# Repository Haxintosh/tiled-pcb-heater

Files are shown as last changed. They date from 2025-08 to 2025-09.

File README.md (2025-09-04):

render of the power distribution PCB
# Tiled 3D printing bed
This project is a scalable, Klipper-compatible heated bed system designed for efficiency and flexibility. The bed is built from PCB-based heater tiles (≈100W each) that can be individually powered, allowing selective heating to reduce energy use. A central hub board, driven by an STM32 microcontroller, controls up to multiple channels with individual MOSFET switching and thermistor sensing.  

The project consists of 2 types of PCBs, the tiles and the power distribution boards.  

Currently there is a 150mm tile and a 8 channel power distribution board.  

## Images
Heater tile:  
render of the tile  
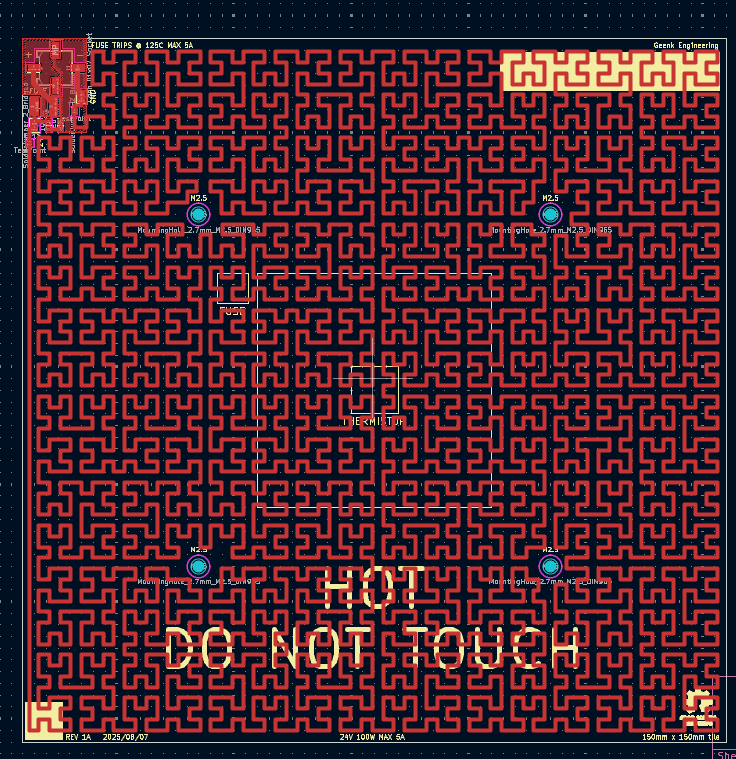
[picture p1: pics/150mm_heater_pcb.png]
image of the pcb
  
Power distribution board:  
render of the power distribution PCB  
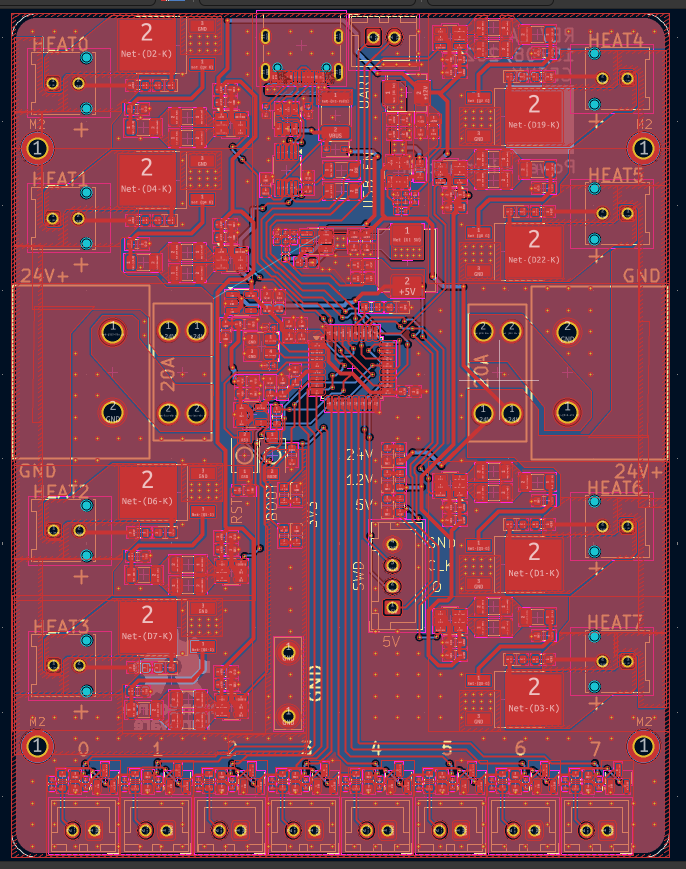
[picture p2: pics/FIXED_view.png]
image of the pd pcb
  

## Specs
The calculator can found here: https://www.desmos.com/calculator/dyaic1mb9s  

Per tile:
| Measurements 	| Value 	|
|---	|---	|
| Dimensions 	| 150mm x 150mm 	|
| Power			| ~110W @ 24v 	|
| Max Temp		| ~105°C*			|

> [!WARNING]
> The max operating temperature depends on the rated temperature of the connector. The thermal fuse blows at around 125°C to prevent thermal runaway, but the current chosen connector (MicroFit 3) is only rated to 105°C.

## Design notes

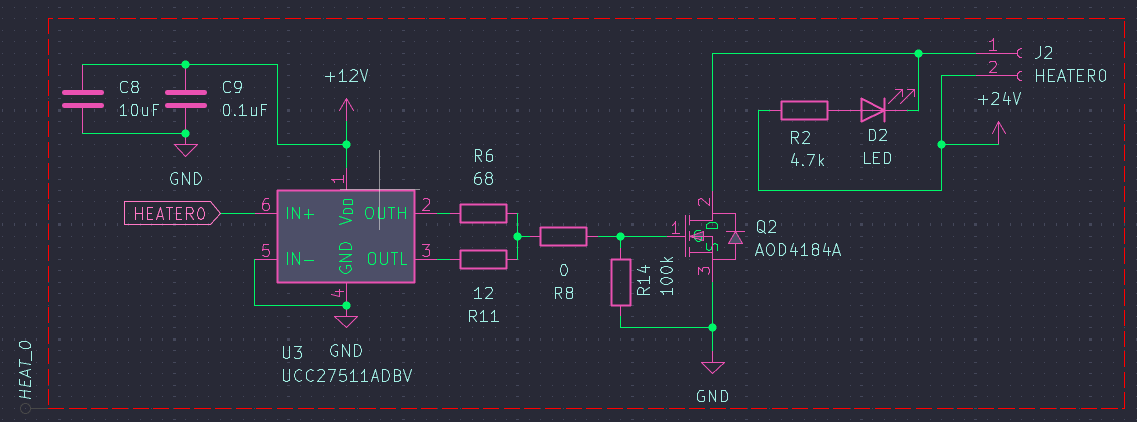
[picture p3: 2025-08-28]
pics/labeled.png

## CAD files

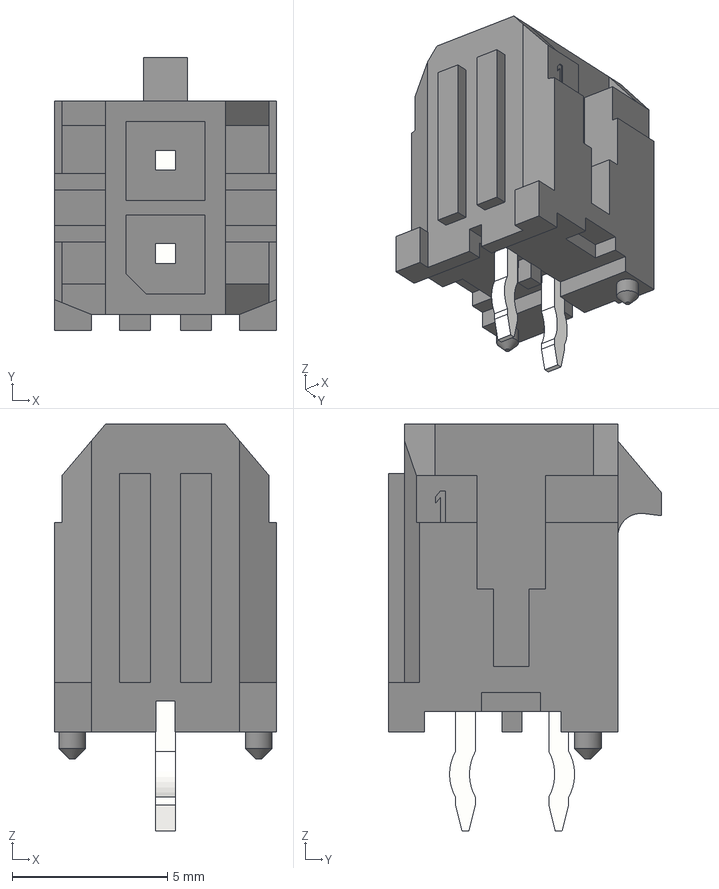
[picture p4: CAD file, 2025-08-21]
src/power distribution/3d/430450212.step
7.15 x 8.77 x 13.1 mm

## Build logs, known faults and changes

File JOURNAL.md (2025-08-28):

---
Title: "Modular 3D printing bed"
Author: "Geenk"
Description: "A modular and scalable 3D printing heated bed system."
Created On: "7/8/2025"
---

# 2025-08-07 Log 1: Initial planning & research
Time: 30min  
Started the project and laid out the project's main criteria. The project is a Klipper compatible scalable and modular heated bed system. The tile nature of the beds allows the printer to selectively heat areas to reduce power consumption. The heated beds are made of individual tiles of PCB-based resistive heaters, which are connected to a power distribution board/hub. The hub, in turn, is connected to Klipper via UART over USB and is able to control 8 tiles of around 100W each. Each tile is connected through a connector for power and another one for thermistor (maybe add a connector on the tile for a thermistor to allow for a single cable from tile to hub? interference). To calculate the length and the width of the trace required for a given wattage, I've found and used the trace resistance formula and put it in a Desmos calculator (https://www.desmos.com/calculator/dyaic1mb9s).   
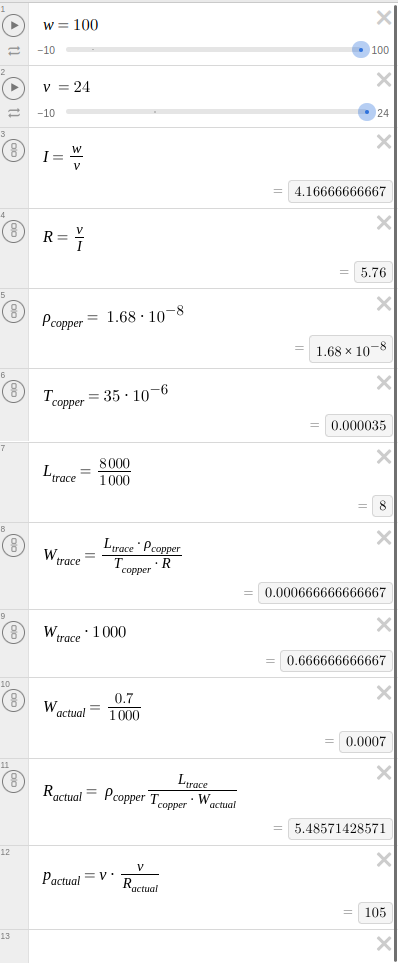
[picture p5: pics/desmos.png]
desmos image of trace width and height calculations


# 2025-08-07 Log 2: Heated bed schematic
Time: 30min  
Finished the schematic of the heated bed. I've decided to add in a thermal fuse in series with the 24V input to prevent the heater to go into thermal runaway. I have also added a LED to indicate when the plate is being powered. It was hard to figure out a way to connect a single trace to 24V and GND without screwing up the nets  of the PCB. I've tried tying 24V and GND but that resulted in everything being named GND and I also tried making the trace resistor into a component, but that didn't work since I needed to modify its' traces for things like screw holes. I finally decided on using solder jumpers to isolate the heater traces. For the connector, I've settled on a Molex MicroFit 3 since some of the connectors are rated up to 125C.   
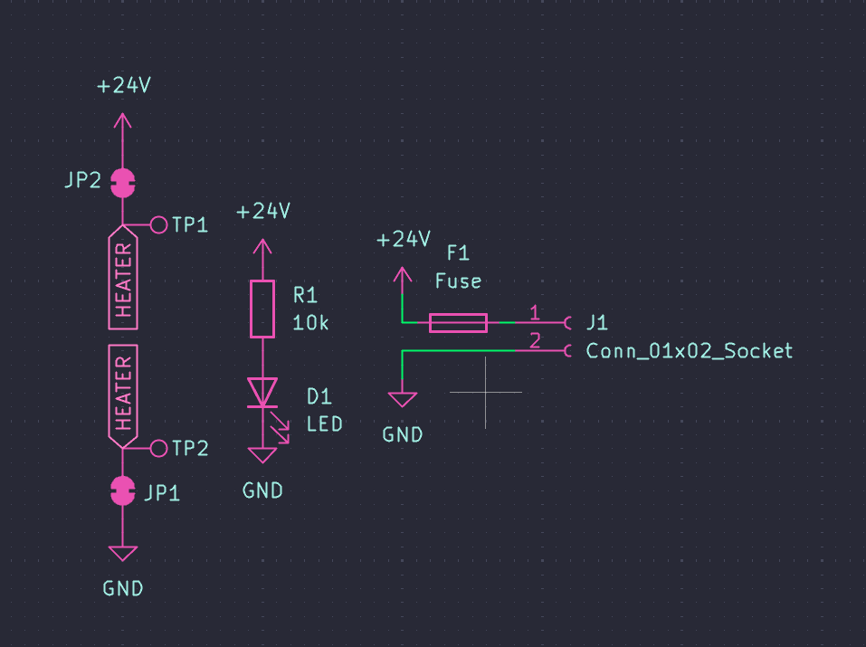
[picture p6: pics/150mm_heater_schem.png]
schematic of the 150mm heated bed
  

# 2025-08-08 Log 3: Heated bed PCB
Time: 1.5h  
Laid out the Hilbert curve heater trace using the KiCad space filling curve plugin, also finished most of the layout of the PCB (LED, connector, fuse). All components and traces are single sided since I plan on going with the aluminum PCB at JLCPCB.  

# 2025-08-08 Log 4: Finalize Heated bed PCB
Time: 1h  
Finalized the heated bed PCB. I added M2.5 holes for mounting and had to move the Hilbert curve traces for hole and countersink clearances. Ran DRC and fixed many errors related to the Hilbert curve since I generated it a bit too big. I added also some silkscreen texts.  
PCB image of the heated bed PCB
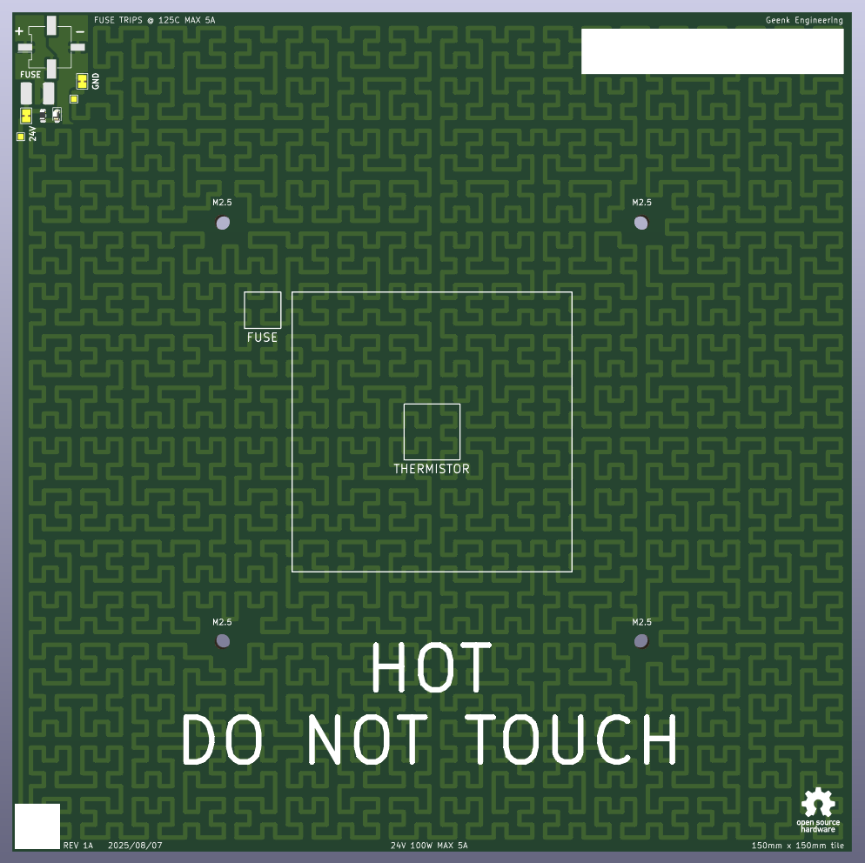
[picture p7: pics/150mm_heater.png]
rendered image of the heated bed PCB
  
# 2025-08-11 Log 5: Power distribution schematic (MCU + MOSFET drivers)
Time: 2h  
Started the schematic for the power hub board. The board is made up of 4 main sections, the MCU, STM32F030K, was chosen due to its analog input multiplexing capabilities and its ease of integration with Klipper, the MOSFET switching, made up of a gate driver and a N channel MOSFET capable of handling up to 5A of current with safety margins, the thermistor sensing section, and finally the voltage rails. I've finished most of the MCU section, with the UART to USB converter, the crystal oscillators, and the pinout of the MCU. I've also done the MOSFETs, where each one is controller by a driver IC and there's 8 channels of switching. It was my first time working with STM32 chips but it was easier than I thought.  
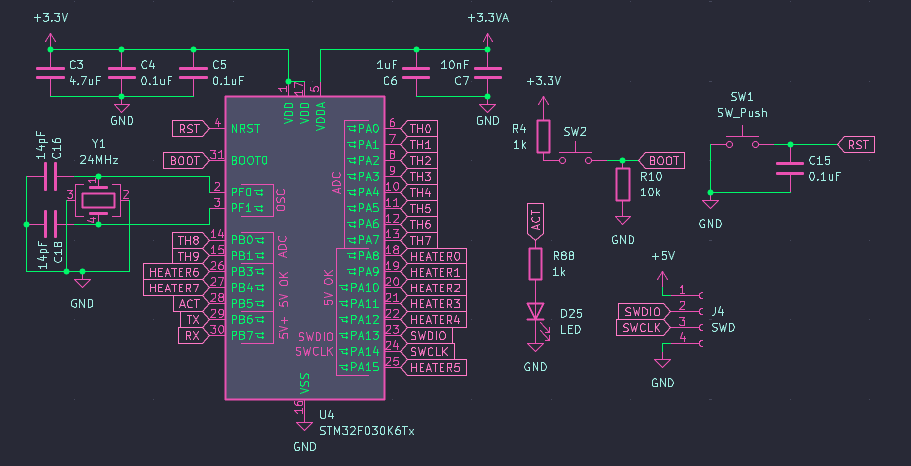
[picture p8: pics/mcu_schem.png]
schematic of the STM32 MCU

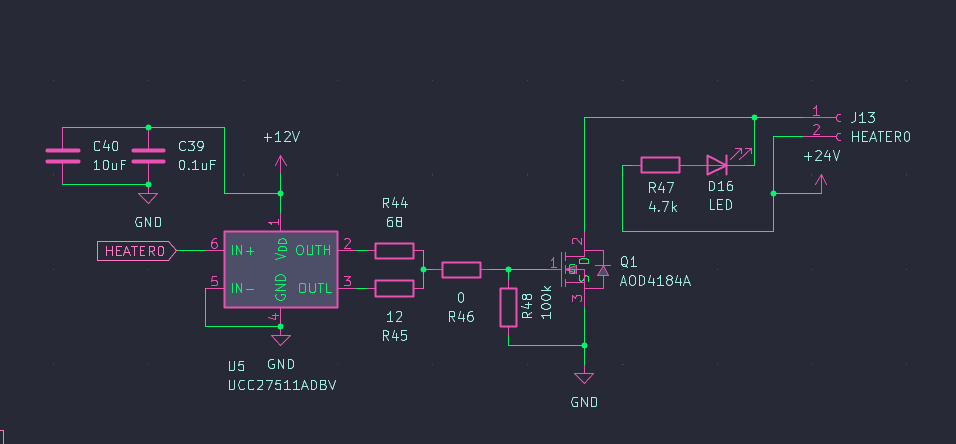
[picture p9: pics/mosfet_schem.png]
schematic of the MOSFET and the gate driver
  

# 2025-08-12 Log 6: Power distribution schematic (thermistor sensing, power rails, and a bit of clean up)
Time: 2h  
Finished up the schematic for the power distribution board. I've added in the thermistor sensing section and the voltage rails needed to power the board. Also added some protection in the form of a polyfuse on the USB rails and one fuse on each of the 24V input rail just in case. The thermistor sensing as derived from the BTT SKR mini E3 since it's an established design that  probably will work and I don't wanna spend hours debugging an analog circuit. The power rails are divided up into 24V for the heaters, 12V for gate driver power and allows the MOSFET to fully open, 5V for peripherals and powers the 3V3 rails. The 3V3 rails are divided up into analog 3V3 and digital 3V3 to minimize noise in the thermistor readings.   
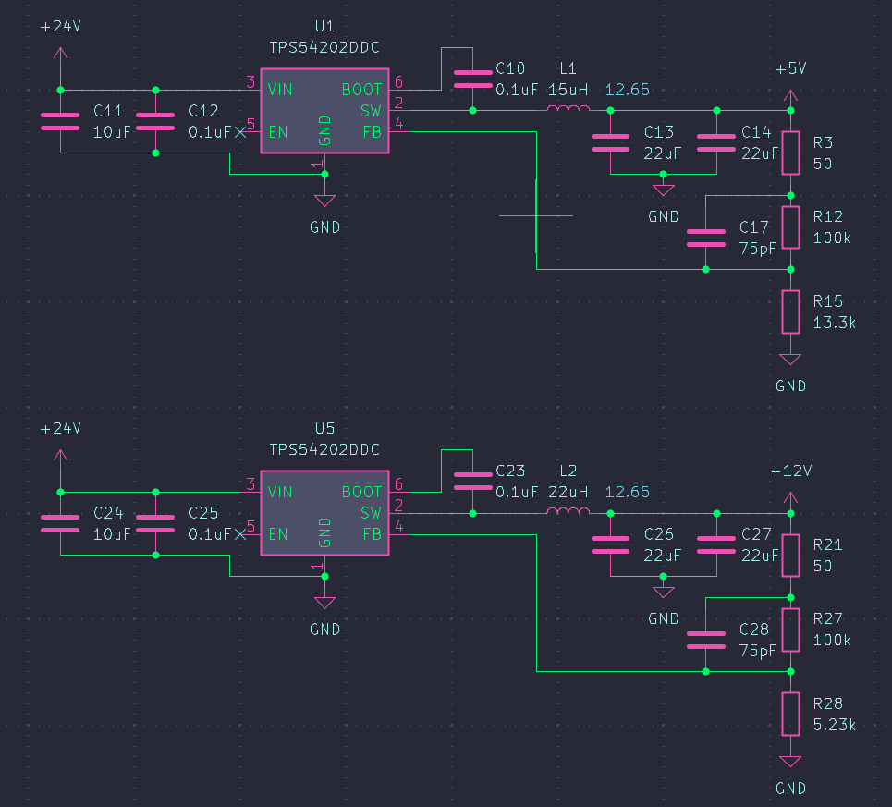
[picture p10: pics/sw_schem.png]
schematic of the switching regulator for the 5V and 12V

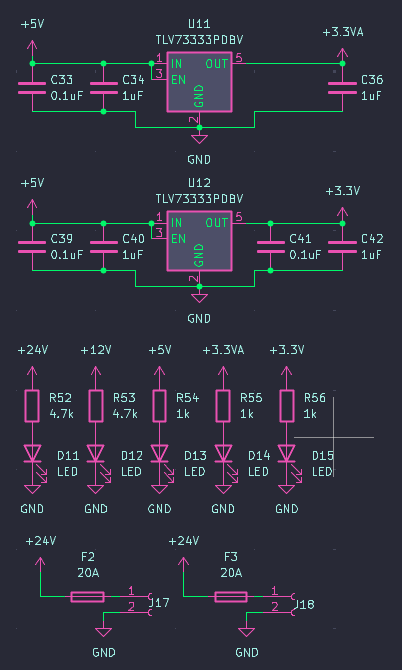
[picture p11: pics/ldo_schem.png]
schematic of the LDOs and led indicator for power

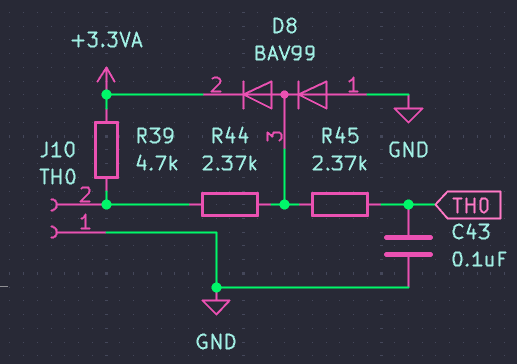
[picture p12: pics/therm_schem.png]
schematic of the thermistor sensing section
  

# 2025-08-16 Log 7: MOSFET channel placement  
Time: 3.5h  
Started on the PCB layout for the power distribution board. The idea was to have 4 outputs on the left and right side of the PCB with a power input screw terminal in the middle of the 4 outputs. I thought I could save time by using the multichannel placement tools recently added to KiCad, but I didn't know how to use it at first for sheets without hierarchical sheets. But after 30min of experimentation, I figured it out and annotated the schematic with rule areas and directive labels. Then, I routed laid out a MOSFET switching channel, making sure there's plenty of thermal mass in the copper planes surrounding the MOSFET to take away the heat for thermal management. Then, after finishing a single channel, I've replicated the single channel design to 3 other channels for the left side. I've then moved them around a bit to fit the power connector in the middle. Then I had to extend some of the copper planes to connect the other channels. I then did the same for the right side.   
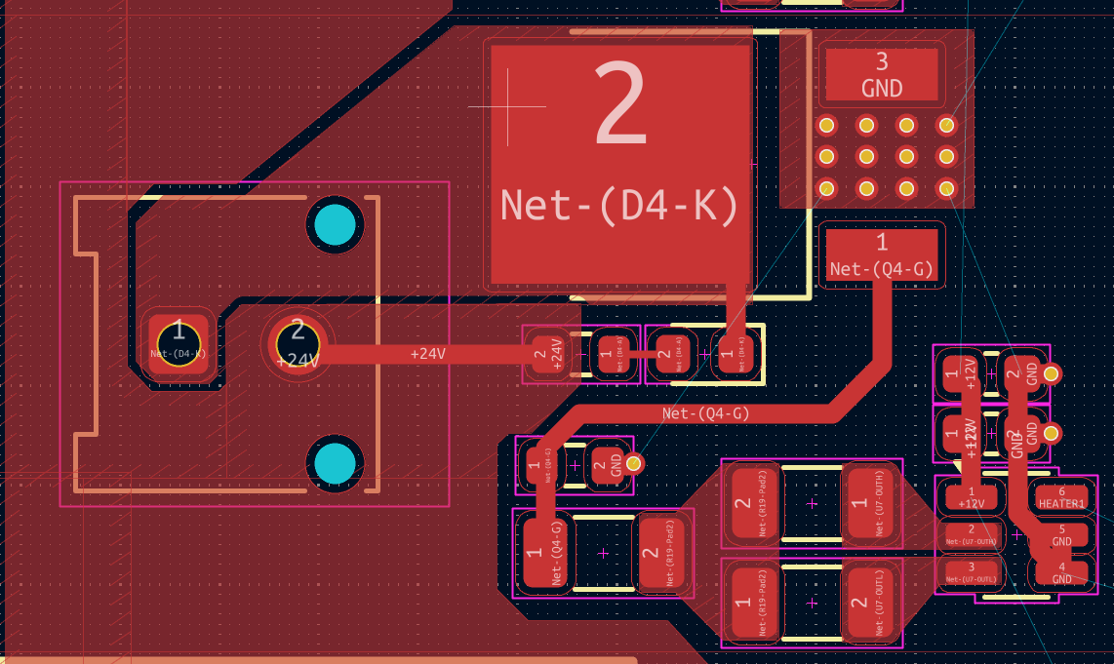
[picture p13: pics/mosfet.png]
image of a single MOSFET layout

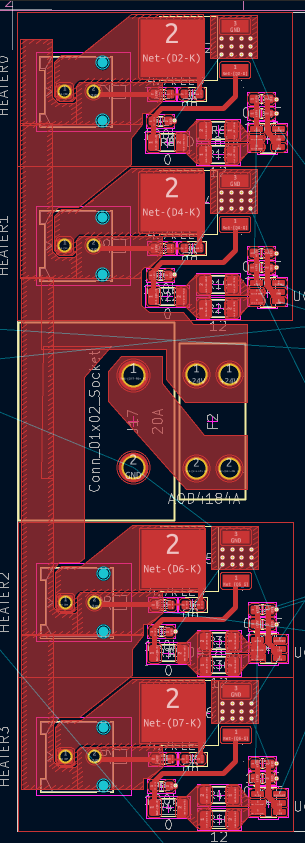
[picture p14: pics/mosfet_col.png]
image of the complete MOSFET layout for the left


# 2025-08-17 Log 8: USB, protection and UART-USB
Time: 1h  
Laid out the PCB for the USB C connector and the ESD protection circuitry, Also routed the polyfuse. The layout for the UART to USB was also done. I included a connector and some 0 Ohm resistors in series with the UART bus for a direct Klipper UART connection option.  
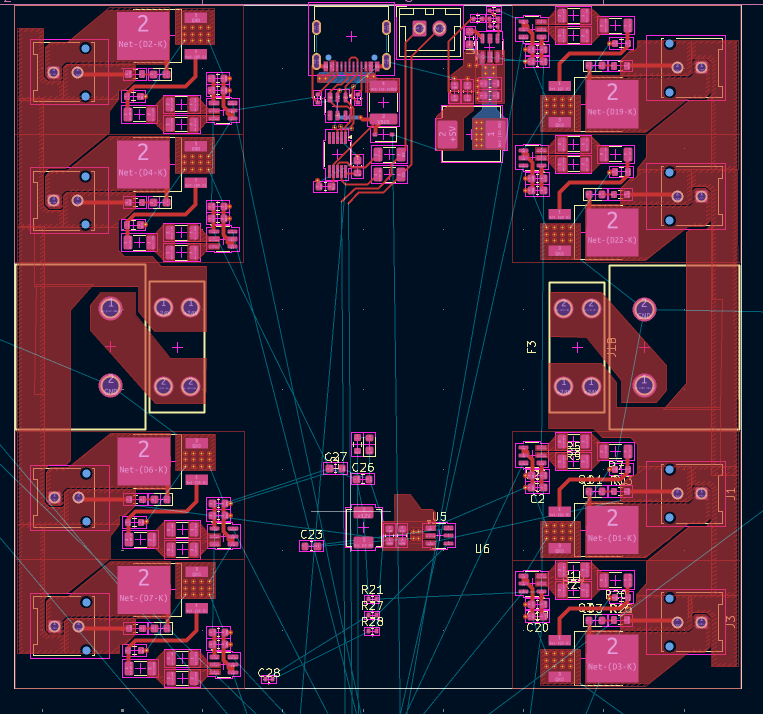
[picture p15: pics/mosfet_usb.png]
image of the whole PCB with the MOSFET layout and USB layout on top
  

# 2025-08-18 Log 9: Power regulation
Time: 1.5h  
Laid out the traces for the voltage regulators. The 5V and 12V rails are converters from 24V using switching regulators. I had to plan things out with the MCU to not interfere with the analog traces especially given the high noises originating from tshe switching regulators. The feedback resistors were placed far away from the switching nodes and most of the layout followed the recommended layout by TI.   

# 2025-08-18 Log 10: STM32
Time: 1.5h  
Placed the MCU in the middle of the board, with the sensitive analog pins facing towards to bottom of the board and away from the switching regulators. Then the decoupling capacitors were placed along side the crystal oscillator. I then placed the 2 LDOs regulating the 3V3 rails quite close to the STM32 since there weren't many places left for them. I then connected the PWM control signals for the MOSFETs. I originally thought that the PWM traces from the MCU will cause a good amount of noise, but apparently Klipper uses a 10Hz signal to control   the heaters. 
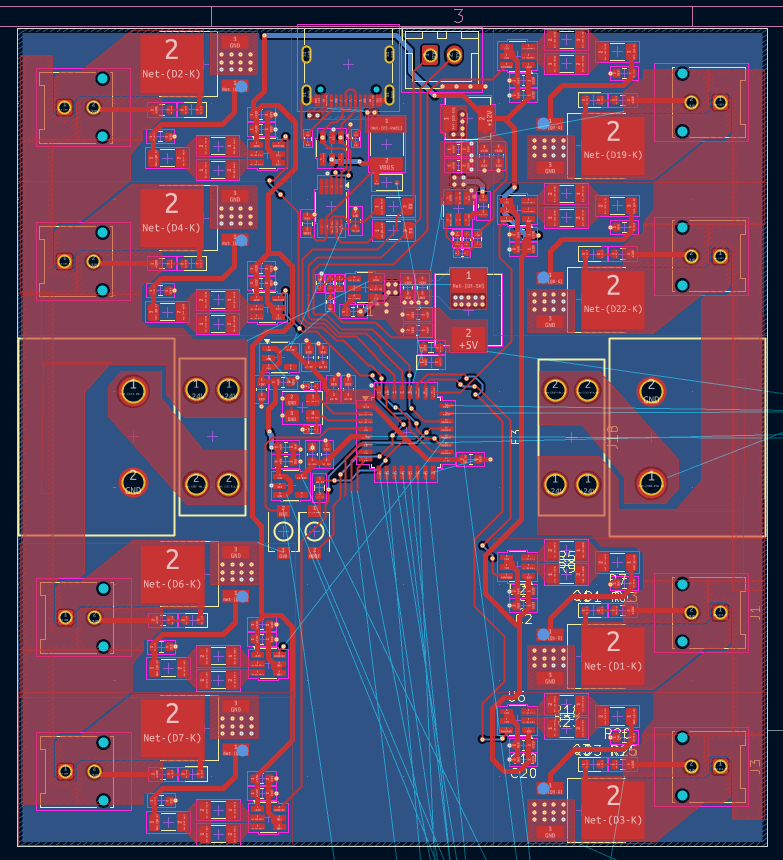
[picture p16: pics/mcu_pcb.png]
image of the whole PCB with the MCU section done


# 2025-08-20 Log 11: Thermistor & DRC
Time: 2h   
Routed the thermistor sensing section on the PCB and replicated the layout for the other 7 channels. Then routed from the MCU to the channels. I've also placed the SWD connector for debugging and for flashing just in case the USB flashing fails. I've also added a test hook for oscilloscope ground for probing purpose. I've also added some M2 screw mount holes on the 4 corners of the PCB and silkscreen labels for the different inputs and LEDs. I finished by rounding out the corners of the PCB and ran & fixed DRC.  
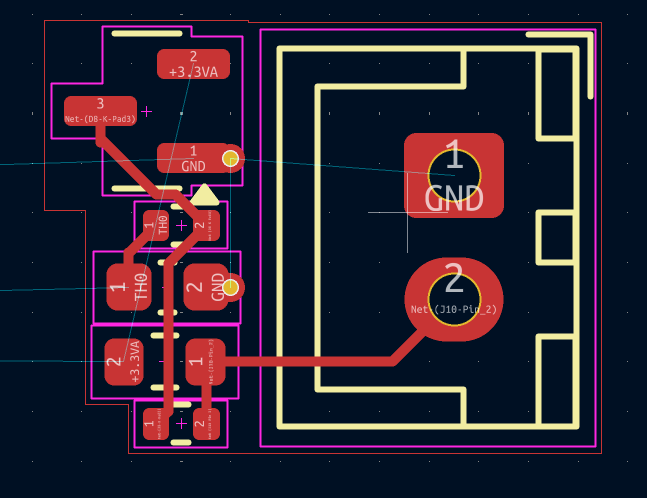
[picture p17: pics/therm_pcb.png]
image of the themistor sensing layout

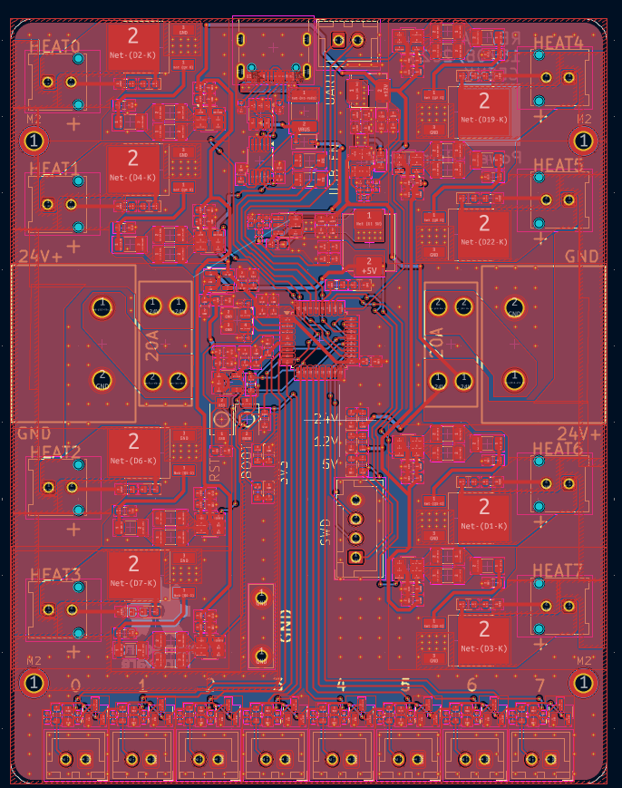
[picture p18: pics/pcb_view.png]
image of the finished PCB


# 2025-08-21 Log 12: UART issue
Time: 30min  
Found out that the for STM32 to flash over USB using a USB-UART converter, the pins PA9/PA10 must be used for UART. I was using a different set of pins, meaning that I would not be able to flash the STM32 via USB. I switched and rerouted the HEATER1-2 pins with the UART RX/TX pins.   
image of the fixed PCB
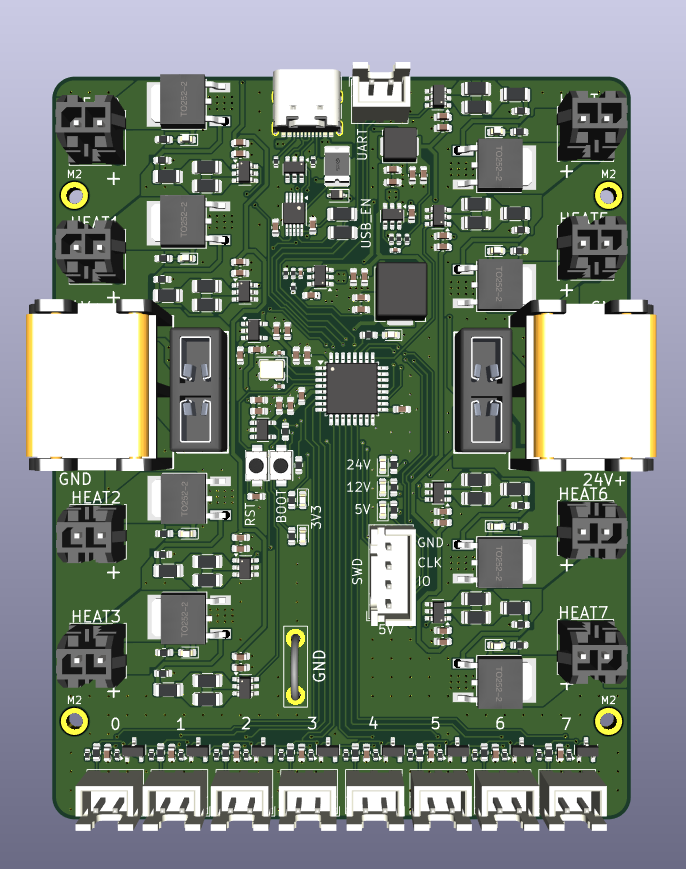
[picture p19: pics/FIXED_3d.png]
image of a 3D view of the PCB


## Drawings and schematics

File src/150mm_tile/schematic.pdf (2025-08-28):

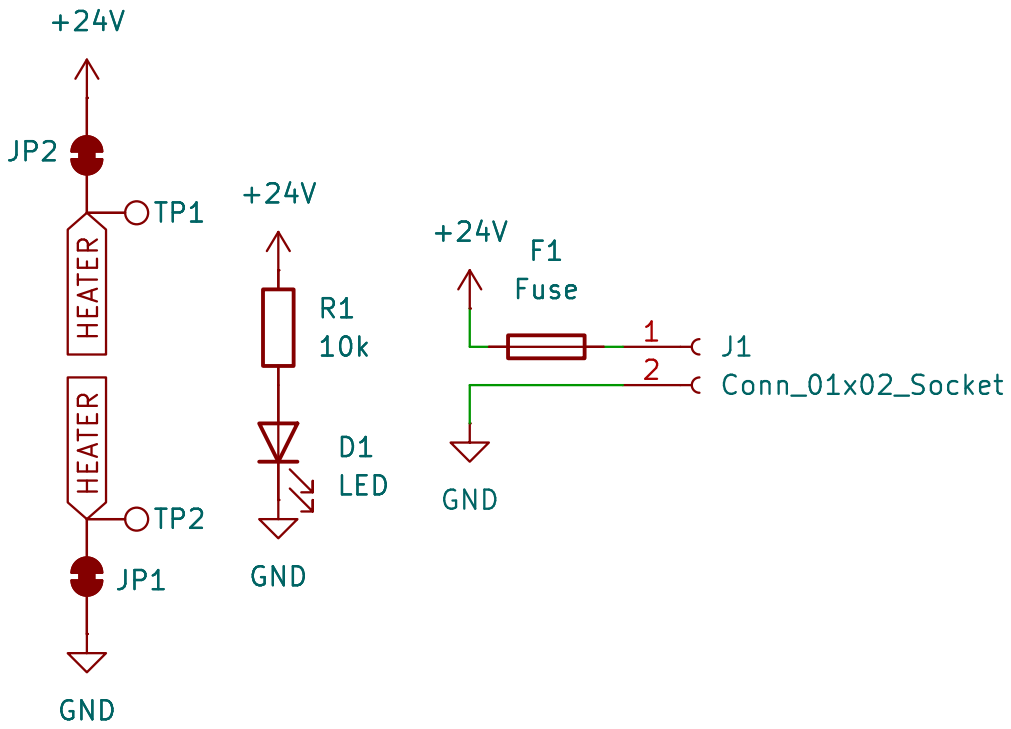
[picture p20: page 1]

Id: 1/1 Title: File: pcb-heater.kicad_sch Sheet: /

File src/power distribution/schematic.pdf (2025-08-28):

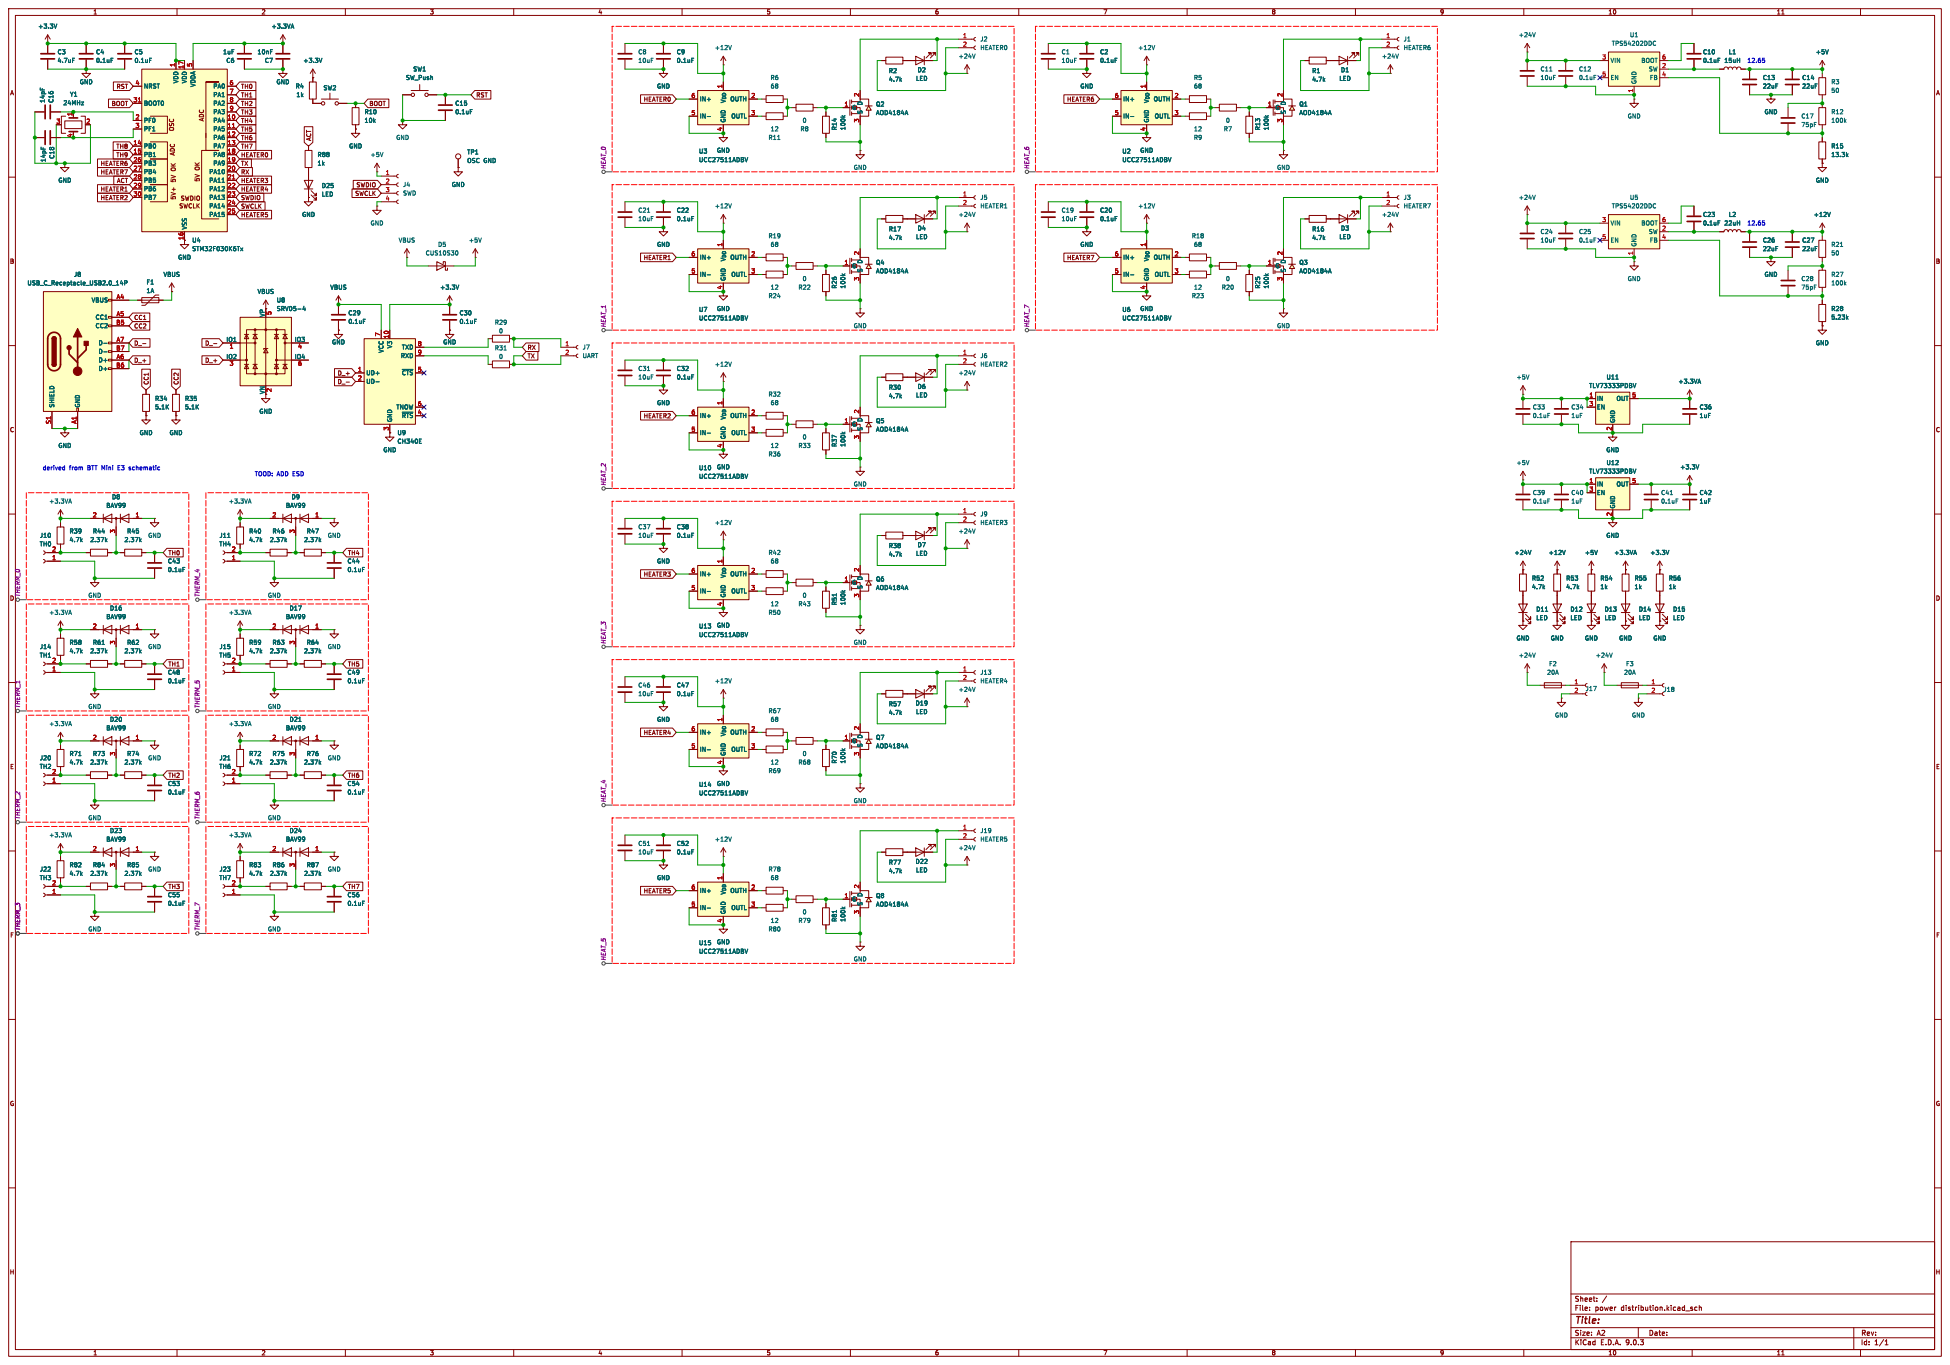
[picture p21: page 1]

TH8 BOOT
SWDIO5V OK ADC
LED OSC ADC 5V OK 5V+ SWCLK

derived from BTT Mini E3 schematic

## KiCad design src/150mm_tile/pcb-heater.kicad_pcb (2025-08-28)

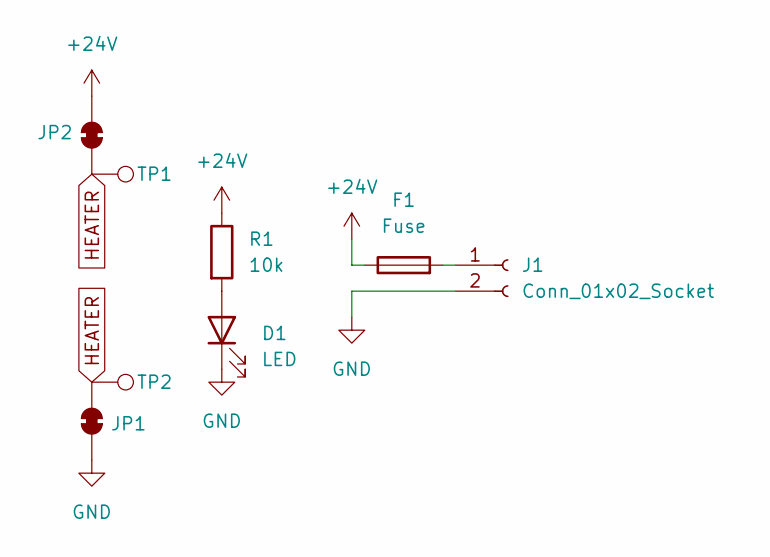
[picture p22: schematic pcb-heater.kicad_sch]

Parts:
D1: LED; LED_0603_1608Metric
F1: Fuse; thermal fuse
J1: Conn_01x02_Socket; Molex_Micro-Fit_3.0_43045-0218_2x01-1MP_P3.00mm_Vertical
JP1, JP2: SolderJumper_2_Bridged; SolderJumper-2_P1.3mm_Bridged_Pad1.0x1.5mm
R1: 10k; R_0603_1608Metric
TP1, TP2: TestPoint; TestPoint_Pad_1.0x1.0mm

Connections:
+24V: F1.1, JP2.1 (A), R1.1
GND: D1.1 (K), J1.2, JP1.1 (A)
HEATER: JP1.2 (B), JP2.2 (B), TP1.1, TP2.1
unnamed: D1.2 (A), R1.2
unnamed: F1.2, J1.1, J1.MP

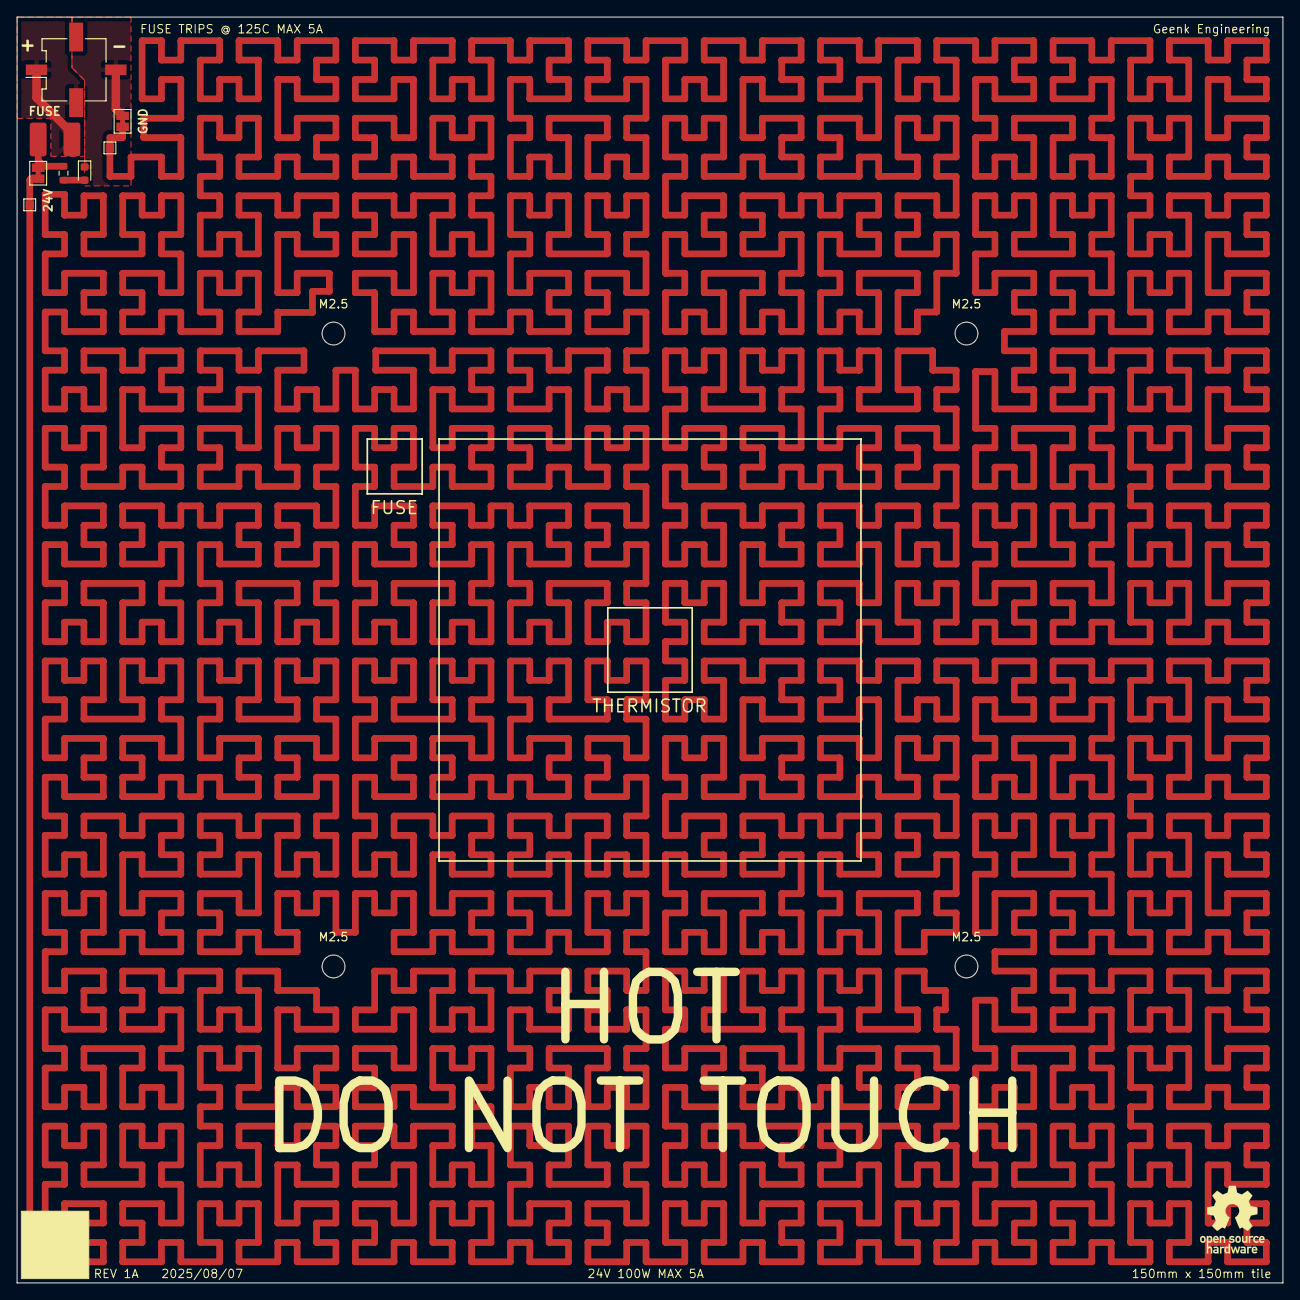
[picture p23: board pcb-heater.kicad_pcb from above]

Board: 2 copper layers, 150.0 x 150.0 mm, 12 parts (0 on the bottom side), 5 nets.

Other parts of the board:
M2.5, M2.5#2, M2.5#3, M2.5#4: MountingHole_2.7mm_M2.5_DIN965

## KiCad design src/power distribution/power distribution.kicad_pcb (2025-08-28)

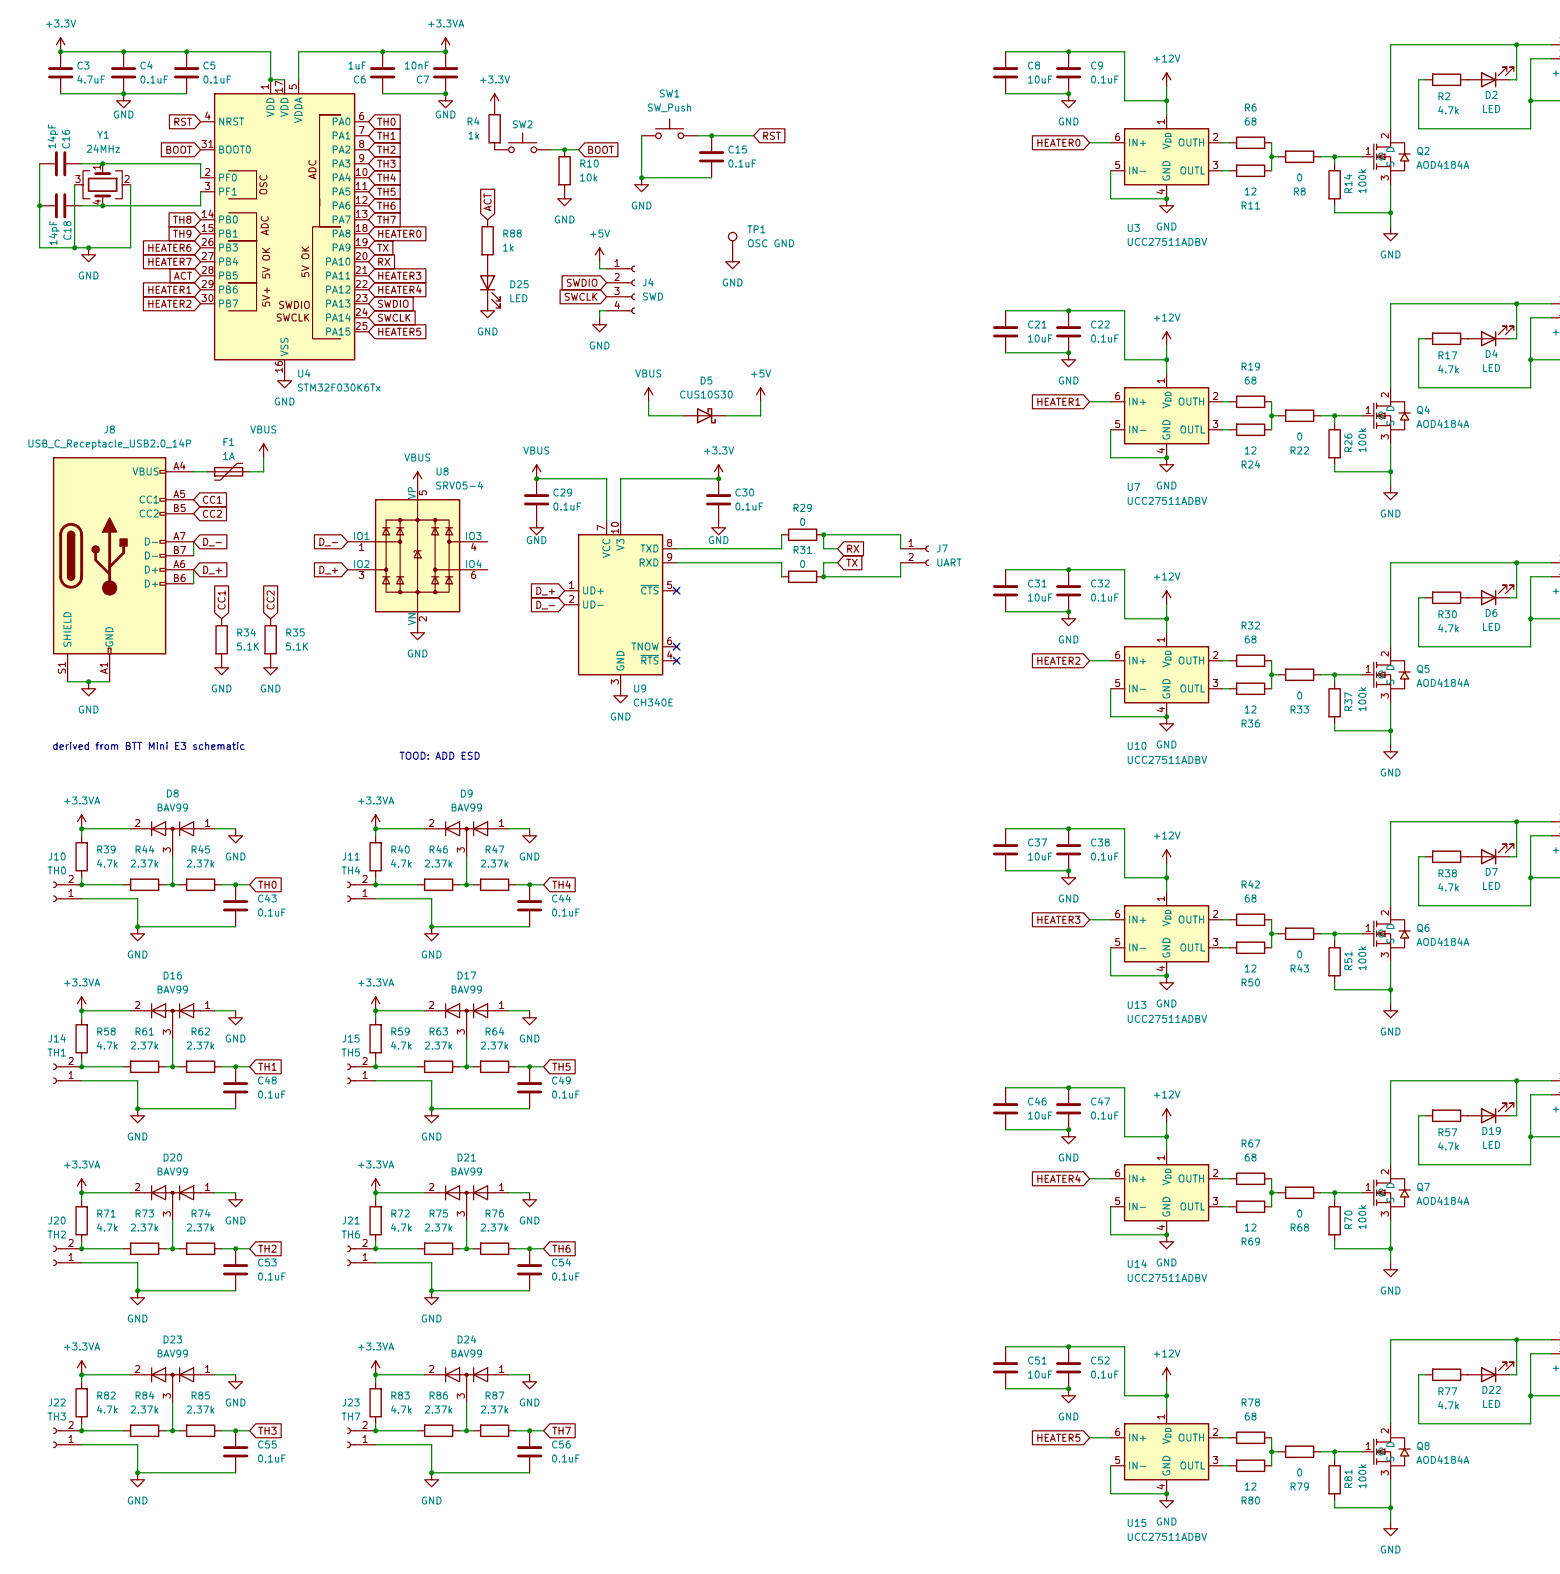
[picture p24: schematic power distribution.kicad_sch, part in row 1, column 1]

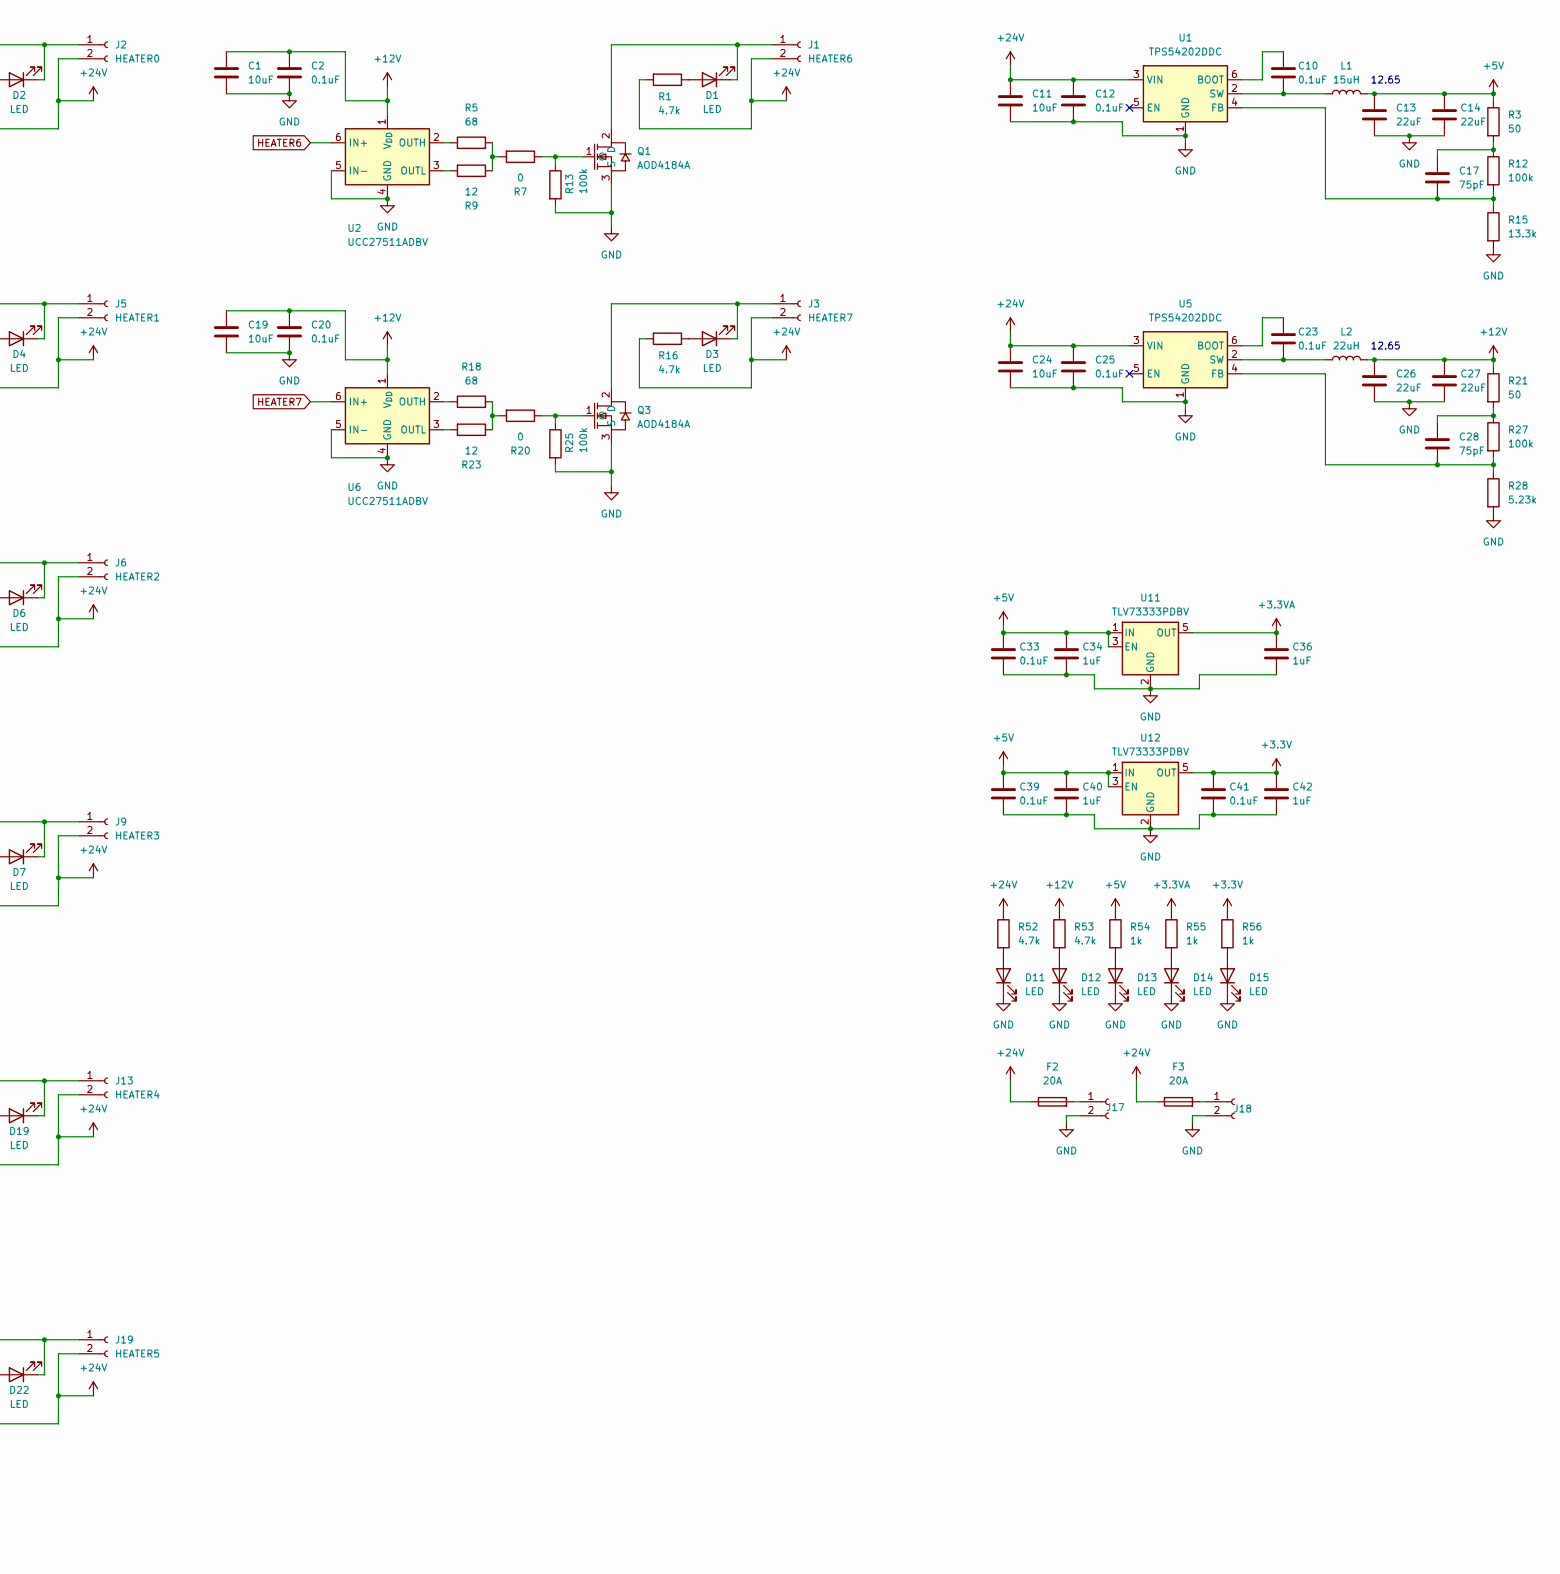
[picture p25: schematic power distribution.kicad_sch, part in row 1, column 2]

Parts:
C1, C8, C11, C19, C21, C24, C31, C37, C46, C51: 10uF; C_0603_1608Metric
C2, C4, C5, C9, C10, C12, C15, C20, C22, C23, C25, C29, C30, C32, C33, C38, C39, C41, C43, C44, C47, C48, C49, C52, C53, C54, C55, C56: 0.1uF; C_0603_1608Metric
C3: 4.7uF; C_0603_1608Metric
C6, C34, C36, C40, C42: 1uF; C_0603_1608Metric
C7: 10nF; C_0603_1608Metric
C13, C14, C26, C27: 22uF; C_0603_1608Metric
C16, C18: 14pF; C_0402_1005Metric
C17, C28: 75pF; C_0402_1005Metric
D1, D2, D3, D4, D6, D7, D11, D12, D13, D14, D15, D19, D22, D25: LED; LED_0603_1608Metric
D5: CUS10S30; D_SOD-323; lcsc C146335
D8, D9, D16, D17, D20, D21, D23, D24: BAV99; SOT-23
F1: 1A; C_1812_4532Metric; lcsc C2649901
F2, F3: 20A; FUSE-TH_4P-L16.0-W6.7
J1: HEATER6; Molex_Micro-Fit_3.0_43045-0212_2x01_P3.00mm_Vertical
J2: HEATER0; Molex_Micro-Fit_3.0_43045-0212_2x01_P3.00mm_Vertical
J3: HEATER7; Molex_Micro-Fit_3.0_43045-0212_2x01_P3.00mm_Vertical
J4: SWD; JST_XH_B4B-XH-A_1x04_P2.50mm_Vertical
J5: HEATER1; Molex_Micro-Fit_3.0_43045-0212_2x01_P3.00mm_Vertical
J6: HEATER2; Molex_Micro-Fit_3.0_43045-0212_2x01_P3.00mm_Vertical
J7: UART; JST_XH_B2B-XH-A_1x02_P2.50mm_Vertical
J8: USB_C_Receptacle_USB2.0_14P; USB_C_Receptacle_G-Switch_GT-USB-7010ASV
J9: HEATER3; Molex_Micro-Fit_3.0_43045-0212_2x01_P3.00mm_Vertical
J10: TH0; JST_XH_B2B-XH-A_1x02_P2.50mm_Vertical
J11: TH4; JST_XH_B2B-XH-A_1x02_P2.50mm_Vertical
J13: HEATER4; Molex_Micro-Fit_3.0_43045-0212_2x01_P3.00mm_Vertical
J14: TH1; JST_XH_B2B-XH-A_1x02_P2.50mm_Vertical
J15: TH5; JST_XH_B2B-XH-A_1x02_P2.50mm_Vertical
J17, J18: Conn_01x02_Socket; CONN-TH_2P-P9.50_DBT50G-9.5-2P
J19: HEATER5; Molex_Micro-Fit_3.0_43045-0212_2x01_P3.00mm_Vertical
J20: TH2; JST_XH_B2B-XH-A_1x02_P2.50mm_Vertical
J21: TH6; JST_XH_B2B-XH-A_1x02_P2.50mm_Vertical
J22: TH3; JST_XH_B2B-XH-A_1x02_P2.50mm_Vertical
J23: TH7; JST_XH_B2B-XH-A_1x02_P2.50mm_Vertical
L1: 15uH; L_TechFuse_SL0650; lcsc C149585
L2: 22uH; L_Sunlord_MWSA0402S
Q1, Q2, Q3, Q4, Q5, Q6, Q7, Q8: AOD4184A; TO-252-2_L6.6-W6.1-P4.57-LS9.9-TL-CW; LCSC Part C99124
R1, R2, R16, R17, R30, R38, R39, R40, R52, R53, R57, R58, R59, R71, R72, R77, R82, R83: 4.7k; R_0603_1608Metric
R3, R21: 50; R_0402_1005Metric
R4, R54, R55, R56, R88: 1k; R_0603_1608Metric
R5, R6, R18, R19, R32, R42, R67, R78: 68; R_1206_3216Metric
R7, R8, R20, R22, R29, R31, R33, R43, R68, R79: 0; R_1206_3216Metric
R9, R11, R23, R24, R36, R50, R69, R80: 12; R_1206_3216Metric
R10: 10k; R_0603_1608Metric
R12, R27: 100k; R_0402_1005Metric
R13, R14, R25, R26, R37, R51, R70, R81: 100k; R_0603_1608Metric
R15: 13.3k; R_0402_1005Metric
R28: 5.23k; R_0402_1005Metric
R34, R35: 5.1K; R_0402_1005Metric
R44, R45, R46, R47, R61, R62, R63, R64, R73, R74, R75, R76, R84, R85, R86, R87: 2.37k; R_0402_1005Metric
SW1: SW_Push; SW-SMD_L3.9-W3.0-P4.45
SW2: SW_Push; SW-SMD_L3.9-W3.0-P4.45; lcsc C455280
TP1: OSC GND; TestPoint_Bridge_Pitch7.62mm_Drill1.3mm
U1, U5: TPS54202DDC; SOT-23-6
U2, U3, U6, U7, U10, U13, U14, U15: UCC27511ADBV; SOT-23-6
U4: STM32F030K6Tx; LQFP-32_7x7mm_P0.8mm
U8: SRV05-4; SOT-23-6
U9: CH340E; MSOP-10_3x3mm_P0.5mm
U11, U12: TLV73333PDBV; SOT-23-5
Y1: 24MHz; Crystal_SMD_3225-4Pin_3.2x2.5mm

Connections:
+3.3V: C3.1, C4.1, C5.1, C30.1, C41.1, C42.1, R4.1, R56.1, U4.1 (VDD), U4.17 (VDD), U9.10 (V3), U12.5 (OUT)
+3.3VA: C6.2, C7.2, C36.1, D8.2 (A), D9.2 (A), D16.2 (A), D17.2 (A), D20.2 (A), D21.2 (A), D23.2 (A), D24.2 (A), R39.2, R40.2, R55.1, R58.2, R59.2, R71.2, R72.2, R82.2, R83.2, U4.5 (VDDA), U11.5 (OUT)
+5V: C13.1, C14.1, C33.1, C34.1, C39.1, C40.1, D5.1 (K), J4.1, L1.2, R3.1, R54.1, U11.1 (IN), U11.3 (EN), U12.1 (IN), U12.3 (EN)
+12V: C1.1, C2.1, C8.1, C9.1, C19.1, C20.1, C21.1, C22.1, C26.1, C27.1, C31.1, C32.1, C37.1, C38.1, C46.1, C47.1, C51.1, C52.1, L2.2, R21.1, R53.1, U2.1 (V_{DD}), U3.1 (V_{DD}), U6.1 (V_{DD}), U7.1 (V_{DD}), U10.1 (V_{DD}), U13.1 (V_{DD}), U14.1 (V_{DD}), U15.1 (V_{DD})
+24V: C11.1, C12.1, C24.1, C25.1, F2.1, F3.1, J1.2, J2.2, J3.2, J5.2, J6.2, J9.2, J13.2, J19.2, R1.2, R2.2, R16.2, R17.2, R30.2, R38.2, R52.1, R57.2, R77.2, U1.3 (VIN), U5.3 (VIN)
ACT: R88.1, U4.28 (PB5)
BOOT: R10.1, SW2.2, U4.31 (BOOT0)
CC1: J8.A5 (CC1), R34.1
CC2: J8.B5 (CC2), R35.1
D_+: J8.A6 (D+), J8.B6 (D+), U8.3 (IO2), U9.1 (UD+)
D_-: J8.A7 (D-), J8.B7 (D-), U8.1 (IO1), U9.2 (UD-)
GND: C1.2, C2.2, C3.2, C4.2, C5.2, C6.1, C7.1, C8.2, C9.2, C11.2, C12.2, C13.2, C14.2, C15.2, C16.2, C18.2, C19.2, C20.2, C21.2, C22.2, C24.2, C25.2, C26.2, C27.2, C29.2, C30.2, C31.2, C32.2, C33.2, C34.2, C36.2, C37.2, C38.2, C39.2, C40.2, C41.2, C42.2, C43.2, C44.2, C46.2, C47.2, C48.2, C49.2, C51.2, C52.2, C53.2, C54.2, C55.2, C56.2, D8.1 (K), D9.1 (K), D11.1 (K), D12.1 (K), D13.1 (K), D14.1 (K), D15.1 (K), D16.1 (K), D17.1 (K), D20.1 (K), D21.1 (K), D23.1 (K), D24.1 (K), D25.1 (K), J4.4, J8.A1 (GND), J8.A12 (GND), J8.B1 (GND), J8.B12 (GND), J8.S1 (SHIELD), J10.1, J11.1, J14.1, J15.1, J17.2, J18.2, J20.1, J21.1, J22.1, J23.1, Q1.3 (S), Q2.3 (S), Q3.3 (S), Q4.3 (S), Q5.3 (S), Q6.3 (S), Q7.3 (S), Q8.3 (S), R10.2, R13.2, R14.2, R15.2, R25.2, R26.2, R28.2, R34.2, R35.2, R37.2, R51.2, R70.2, R81.2, SW1.1, TP1.1, U1.1 (GND), U2.4 (GND), U2.5 (IN-), U3.4 (GND), U3.5 (IN-), U4.16 (VSS), U4.32 (VSS), U5.1 (GND), U6.4 (GND), U6.5 (IN-), U7.4 (GND), U7.5 (IN-), U8.2 (VN), U9.3 (GND), U10.4 (GND), U10.5 (IN-), U11.2 (GND), U12.2 (GND), U13.4 (GND), U13.5 (IN-), U14.4 (GND), U14.5 (IN-), U15.4 (GND), U15.5 (IN-), Y1.2, Y1.3
HEATER0: U3.6 (IN+), U4.18 (PA8)
HEATER1: U4.29 (PB6), U7.6 (IN+)
HEATER2: U4.30 (PB7), U10.6 (IN+)
HEATER3: U4.21 (PA11), U13.6 (IN+)
HEATER4: U4.22 (PA12), U14.6 (IN+)
HEATER5: U4.25 (PA15), U15.6 (IN+)
HEATER6: U2.6 (IN+), U4.26 (PB3)
HEATER7: U4.27 (PB4), U6.6 (IN+)
unnamed: C17.1, R3.2, R12.1
unnamed: C28.1, R21.2, R27.1
unnamed: D1.2 (A), R1.1
unnamed: D1.1 (K), J1.1, Q1.2 (D)
unnamed: D2.2 (A), R2.1
unnamed: D2.1 (K), J2.1, Q2.2 (D)
unnamed: D3.2 (A), R16.1
unnamed: D3.1 (K), J3.1, Q3.2 (D)
unnamed: D4.2 (A), R17.1
unnamed: D4.1 (K), J5.1, Q4.2 (D)
unnamed: D6.2 (A), R30.1
unnamed: D6.1 (K), J6.1, Q5.2 (D)
unnamed: D7.2 (A), R38.1
unnamed: D7.1 (K), J9.1, Q6.2 (D)
unnamed: D8.3 (K), R44.1, R45.2
unnamed: D9.3 (K), R46.1, R47.2
unnamed: D11.2 (A), R52.2
unnamed: D12.2 (A), R53.2
unnamed: D13.2 (A), R54.2
unnamed: D14.2 (A), R55.2
unnamed: D15.2 (A), R56.2
unnamed: D16.3 (K), R61.1, R62.2
unnamed: D17.3 (K), R63.1, R64.2
unnamed: D19.2 (A), R57.1
unnamed: D19.1 (K), J13.1, Q7.2 (D)
unnamed: D20.3 (K), R73.1, R74.2
unnamed: D21.3 (K), R75.1, R76.2
unnamed: D22.2 (A), R77.1
unnamed: D22.1 (K), J19.1, Q8.2 (D)
unnamed: D23.3 (K), R84.1, R85.2
unnamed: D24.3 (K), R86.1, R87.2
unnamed: D25.2 (A), R88.2
unnamed: F1.1, J8.A4 (VBUS), J8.A9 (VBUS), J8.B4 (VBUS), J8.B9 (VBUS)
unnamed: J10.2, R39.1, R44.2
unnamed: J11.2, R40.1, R46.2
unnamed: J14.2, R58.1, R61.2
unnamed: J15.2, R59.1, R63.2
unnamed: F2.2, J17.1
unnamed: F3.2, J18.1
unnamed: J20.2, R71.1, R73.2
unnamed: J21.2, R72.1, R75.2
unnamed: J22.2, R82.1, R84.2
unnamed: J23.2, R83.1, R86.2
unnamed: Q1.1 (G), R7.1, R13.1
unnamed: Q2.1 (G), R8.1, R14.1
unnamed: Q3.1 (G), R20.1, R25.1
unnamed: Q4.1 (G), R22.1, R26.1
unnamed: Q5.1 (G), R33.1, R37.1
unnamed: Q6.1 (G), R43.1, R51.1
unnamed: Q7.1 (G), R68.1, R70.1
unnamed: Q8.1 (G), R79.1, R81.1
unnamed: R4.2, SW2.1
unnamed: R5.2, R7.2, R9.1
unnamed: R6.2, R8.2, R11.1
unnamed: R18.2, R20.2, R23.1
unnamed: R19.2, R22.2, R24.1
unnamed: R32.2, R33.2, R36.1
unnamed: R42.2, R43.2, R50.1
unnamed: R67.2, R68.2, R69.1
unnamed: R78.2, R79.2, R80.1
unnamed: C10.1, U1.6 (BOOT)
unnamed: C17.2, R12.2, R15.1, U1.4 (FB)
unnamed: C10.2, L1.1, U1.2 (SW)
unnamed: R5.1, U2.2 (OUTH)
unnamed: R9.2, U2.3 (OUTL)
unnamed: R6.1, U3.2 (OUTH)
unnamed: R11.2, U3.3 (OUTL)
unnamed: C16.1, U4.2 (PF0), Y1.1
unnamed: C18.1, U4.3 (PF1), Y1.4
unnamed: C23.1, U5.6 (BOOT)
unnamed: C28.2, R27.2, R28.1, U5.4 (FB)
unnamed: C23.2, L2.1, U5.2 (SW)
unnamed: R18.1, U6.2 (OUTH)
unnamed: R23.2, U6.3 (OUTL)
unnamed: R19.1, U7.2 (OUTH)
unnamed: R24.2, U7.3 (OUTL)
unnamed: R31.1, U9.9 (RXD)
unnamed: R29.1, U9.8 (TXD)
unnamed: R32.1, U10.2 (OUTH)
unnamed: R36.2, U10.3 (OUTL)
unnamed: R42.1, U13.2 (OUTH)
unnamed: R50.2, U13.3 (OUTL)
unnamed: R67.1, U14.2 (OUTH)
unnamed: R69.2, U14.3 (OUTL)
unnamed: R78.1, U15.2 (OUTH)
unnamed: R80.2, U15.3 (OUTL)
RST: C15.1, SW1.2, U4.4 (NRST)
RX: J7.1, R29.2, U4.20 (PA10)
SWCLK: J4.3, U4.24 (PA14)
SWDIO: J4.2, U4.23 (PA13)
TH0: C43.1, R45.1, U4.6 (PA0)
TH1: C48.1, R62.1, U4.7 (PA1)
TH2: C53.1, R74.1, U4.8 (PA2)
TH3: C55.1, R85.1, U4.9 (PA3)
TH4: C44.1, R47.1, U4.10 (PA4)
TH5: C49.1, R64.1, U4.11 (PA5)
TH6: C54.1, R76.1, U4.12 (PA6)
TH7: C56.1, R87.1, U4.13 (PA7)
TH8: U4.14 (PB0)
TH9: U4.15 (PB1)
TX: J7.2, R31.2, U4.19 (PA9)
VBUS: C29.1, D5.2 (A), F1.2, U8.5 (VP), U9.7 (VCC)

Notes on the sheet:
derived from BTT Mini E3 schematic
12.65
TOOD: ADD ESD

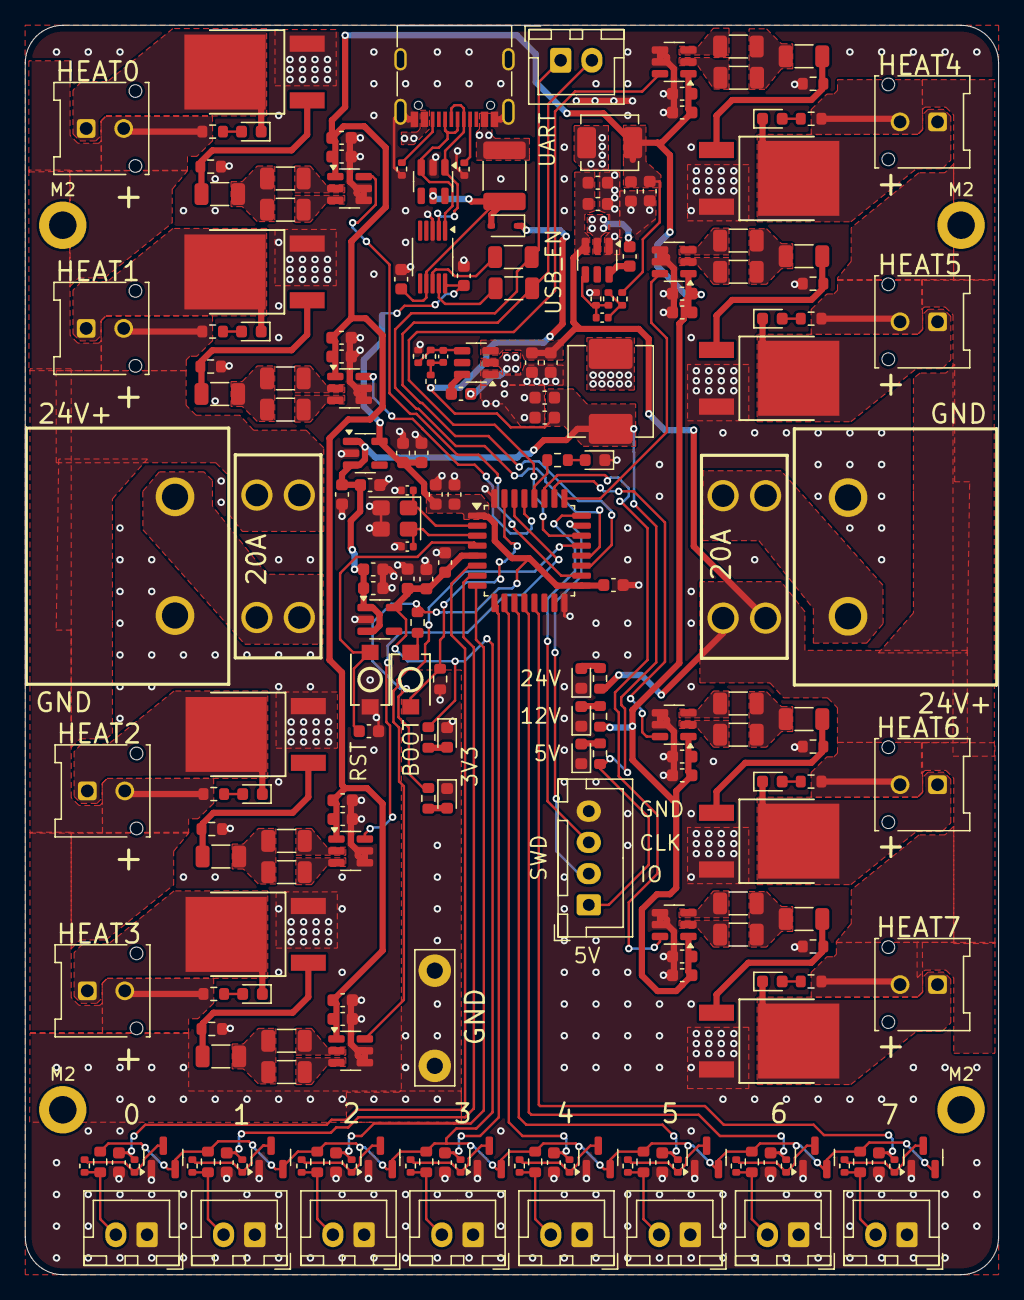
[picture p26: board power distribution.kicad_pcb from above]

Board: 2 copper layers, 77.9 x 100.0 mm, 215 parts (0 on the bottom side), 120 nets.

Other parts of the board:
M2, M2#2, M2#3, M2#4: MountingHole_2.2mm_M2_DIN965_Pad

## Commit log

2025-08-08 milestone: tile pcb done
    [pcb-heater-B_Cu.gbr, pcb-heater-B_Mask.gbr, pcb-heater-B_Paste.gbr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]
2025-08-11 milestone: power distribution schematic done
    [power distribution.kicad_pcb, power distribution.kicad_sch]
2025-08-21 milestone: finished PCB design of the Power Distribution Board
    [430450212.step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]
2025-08-21 fix: fixed uart connections, usb flashing requires flashing via UART on PA9/PA10
    [power distribution.kicad_pcb, power distribution.kicad_sch]
2025-08-27 chore: update github journal with obsidian journal
    [power distribution.kicad_pcb]
2025-08-28 chore: add images
    [power distribution-B_Cu.gbr, power distribution-B_Mask.gbr, power distribution-B_Paste.gbr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]
2025-08-28 chore: cleanuo
    [power distribution.kicad_pcb, power distribution.kicad_sch]
2025-08-28 chore: Add PCB render image to README
    Added an image render of the power distribution PCB to the README.
2025-08-28 chore: update 150mm tile fabrication outputs
    [pcb-heater-B_Cu.gbr, pcb-heater-B_Mask.gbr, pcb-heater-B_Paste.gbr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]
2025-08-28 chore: update for submission
    [430450212.step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]
2025-08-28 chore: remove redundant files
    [430450212.step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]
2025-09-02 chore: add desc
    Expanded project description and added specifications for the heated bed system.
2025-09-04 chore: add heater render image
